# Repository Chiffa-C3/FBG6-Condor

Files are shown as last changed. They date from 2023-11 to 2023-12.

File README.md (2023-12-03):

# Проект печатной головы "Кондор" 

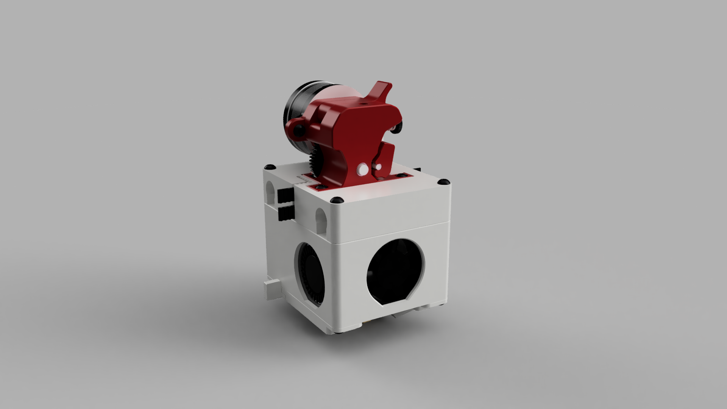
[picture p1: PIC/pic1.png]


Проект печатной головы для принтера FBG6 с поддержкой [Klicky-Probe](https://github.com/jlas1/Klicky-Probe) и фидером на основе Mini Stealthburner с быстрым отжимом филамента для более легкой замены прутка.

Используемые детали:
- Стоковый радиатор FBG6
- Гладкое биметалическое горло 21мм
- Турбинки 4010 GDSTime
- Вентилятор 3010 GDSTime
- Набор BMG шестерней [пример](https://aliexpress.ru/item/1005003334389217.html)
- Шаговый двигатель Nema 14 36STH20 [пример](https://aliexpress.ru/item/1005002717890067.html?sku_id=12000031330274970)
- 8шт Круглые магниты 5х5мм
- Микрик [пример](https://aliexpress.ru/item/4001033375208.html)
- Вплавляемые резьбовые латунные вставки М3 4-5мм длины [пример](https://aliexpress.ru/item/1005005372220229.html)

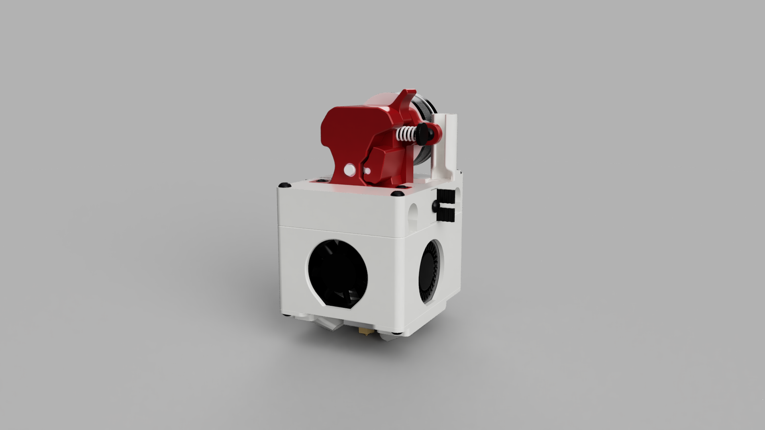
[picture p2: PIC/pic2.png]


- [Сборка проекта](https://github.com/Chiffa-C3/FBG6-Condor/tree/main/Assembly)

- [Настройка Klicky Probe](https://github.com/Chiffa-C3/FBG6-Condor/tree/main/Klicky)

Более подробно о Klicky Probe можно узнать на [странице проекта](https://github.com/jlas1/Klicky-Probe/tree/main)

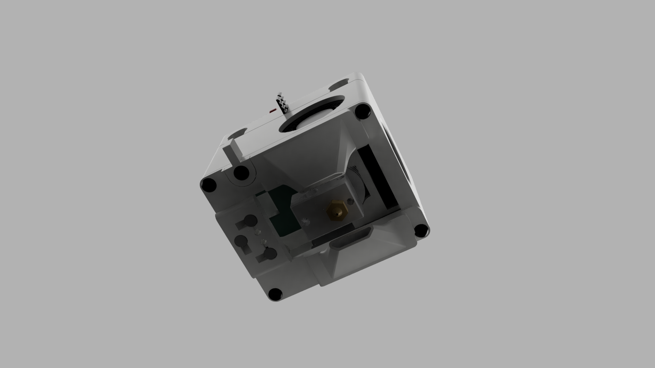
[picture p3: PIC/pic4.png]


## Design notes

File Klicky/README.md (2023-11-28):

# Настройка Klicky

Для датчика Klicky используется пин PC4 и земля.

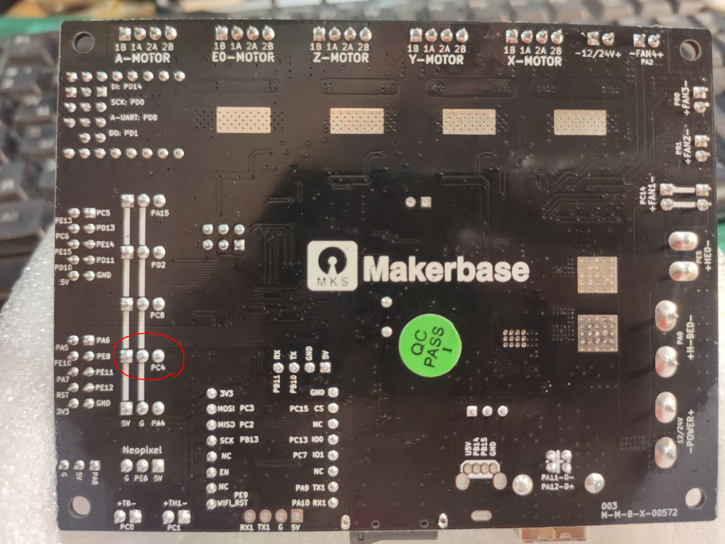
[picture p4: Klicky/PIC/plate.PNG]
plate


Файлы из папки Config скопировать рядом с файлом конфигурации прошивки Klipper `config.cfg`

Заходим в сам файл config.cfg и добавляем в начало 

```
[include klicky-variables.cfg]
[include klicky-macros.cfg]
[include klicky-bed-mesh-calibrate.cfg]
[include klicky-screws-tilt-calculate.cfg]
```

Добавляем в любом месте файла эти блоки настроек

```
[probe]
pin: ^PC4
x_offset: 2.5
y_offset: 30
z_offset: 3.8 # расстояние от кончика сопла до концевика, подбирается калибровкой через скрипт PROBE_CALIBRATE
speed: 5.0
samples: 3
sample_retract_dist: 5.0
samples_result: average
samples_tolerance: 0.1

[bed_mesh]
speed: 60
horizontal_move_z: 5
mesh_min: 7.5, 35
mesh_max: 240, 200
probe_count: 6,4
mesh_pps: 2, 2
algorithm: bicubic
fade_start: 1
fade_end: 10

[screws_tilt_adjust]                     
screw1: 25, 145
screw1_name: back left screw
screw2: 225, 145
screw2_name: back right screw
screw3: 225, 1
screw3_name: front right screw
screw4: 25, 1
screw4_name: front left screw
speed: 200
screw_thread: CW-M4
horizontal_move_z: 10
```

Находим конфигурационный блок под названием `[stepper_z]` и в нем ищем строку `endstop_pin`, комментируем ее знаком # и вставляем ниже `endstop_pin: probe:z_virtual_endstop` чтобы получилось как на примере ниже:
```
#endstop_pin: !PC8
endstop_pin: probe:z_virtual_endstop
```

Настройка позиции док станции для корректировки правильной парковки находится в файле `klicky-variables.cfg`

```
variable_docklocation_x:      168    # X Dock position
variable_docklocation_y:      210    # Y Dock position
```

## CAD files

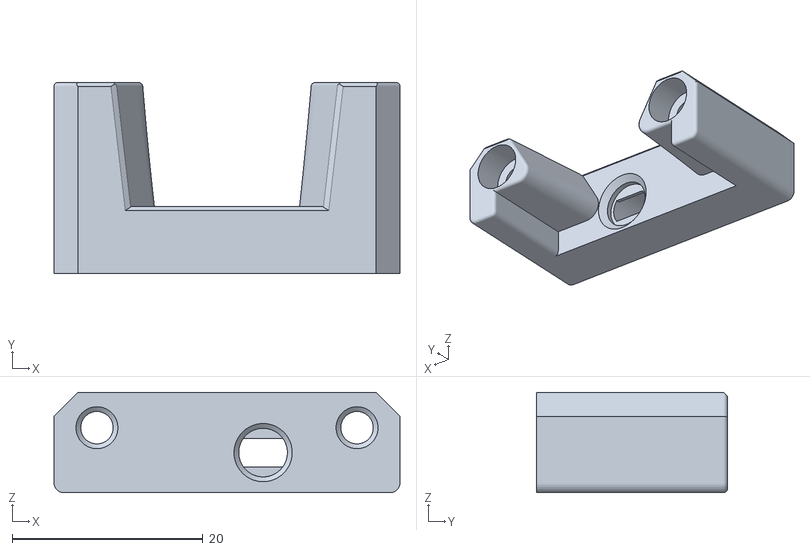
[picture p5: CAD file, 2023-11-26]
STL/Klicky/Probe Dock.stl
36.3 x 20.0 x 10.5

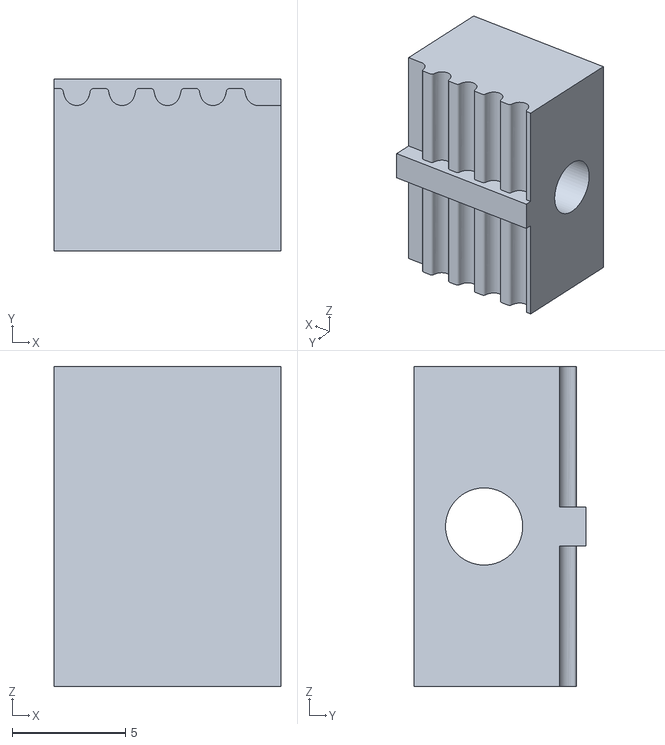
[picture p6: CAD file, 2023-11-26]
STL/Каретка/Крепление ремней.stl
10.0 x 7.60 x 14.1

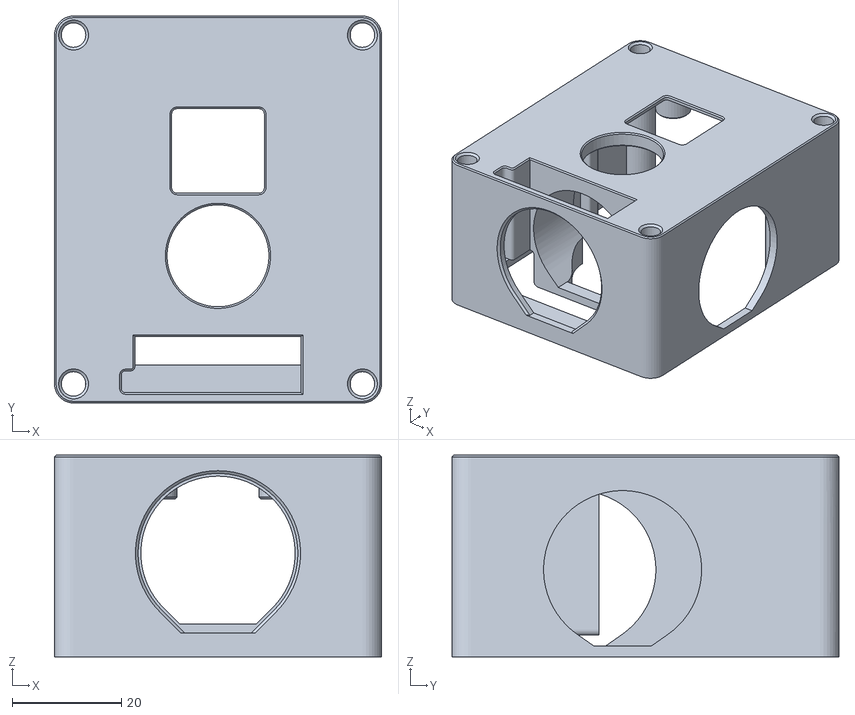
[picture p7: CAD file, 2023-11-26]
STL/Нижняя часть/Блок с вентиляторами.stl
60.0 x 71.0 x 37.0

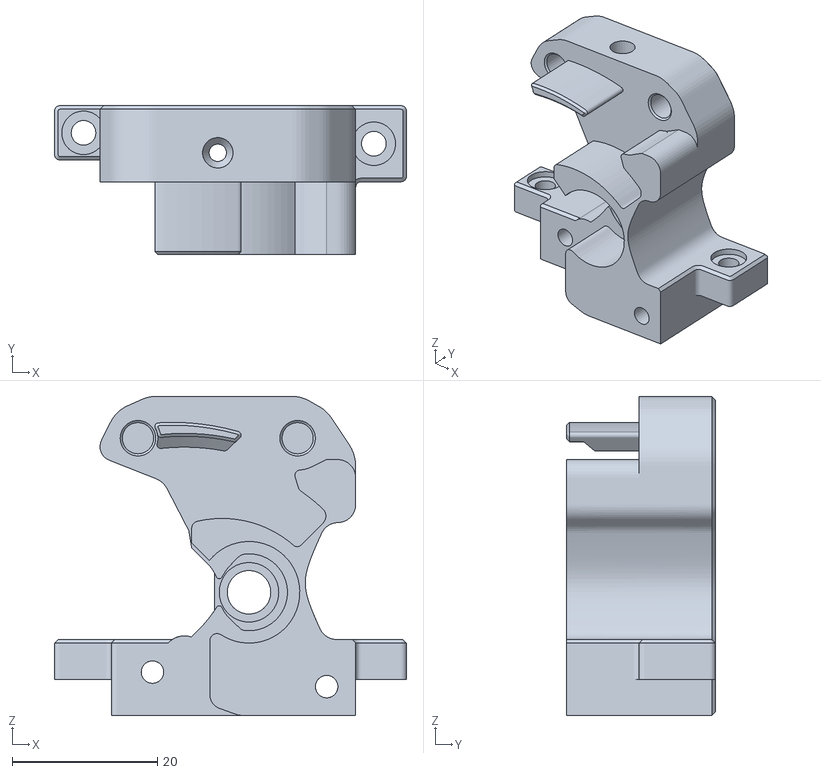
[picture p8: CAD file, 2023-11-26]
STL/Экструдер/Передняя крышка.stl
48.5 x 20.5 x 44.0

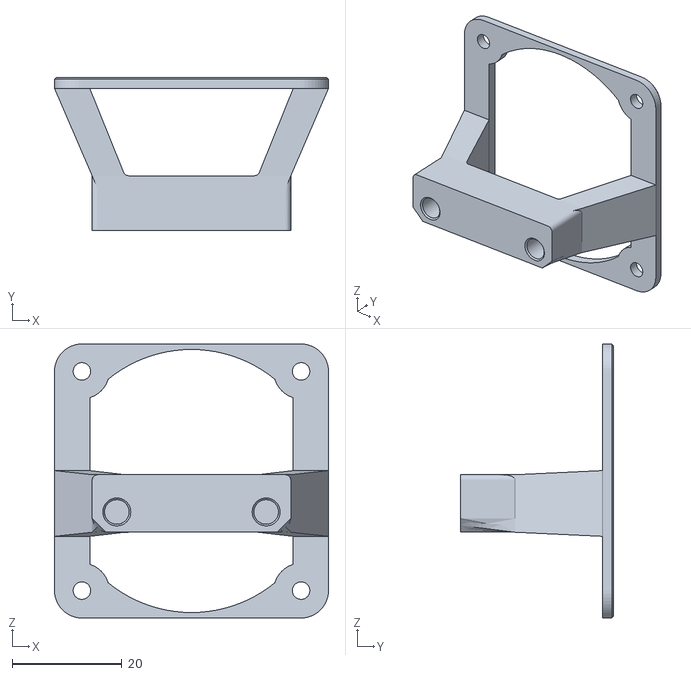
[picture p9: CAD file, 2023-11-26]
STL/Klicky/Крепление на вентилятор.stl
50.0 x 28.0 x 50.0

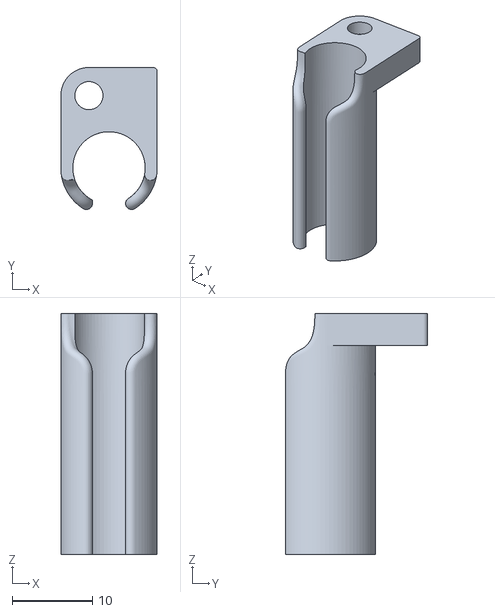
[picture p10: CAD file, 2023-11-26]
STL/Каретка/Держатель косы.stl
12.0 x 17.7 x 30.0

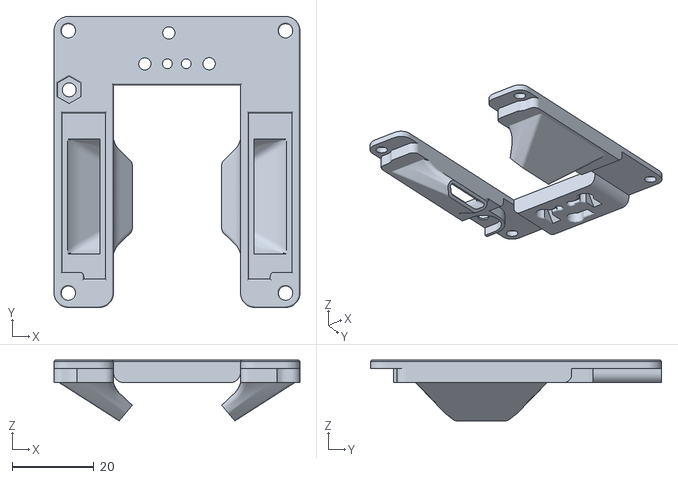
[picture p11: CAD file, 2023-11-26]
STL/Нижняя часть/Обдув.stl
60.0 x 71.0 x 14.9

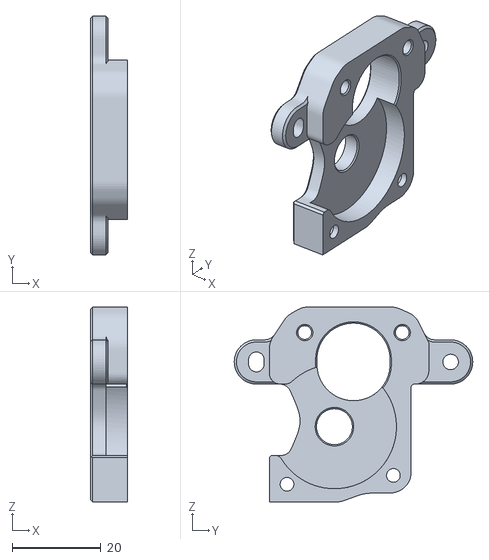
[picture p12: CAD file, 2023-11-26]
STL/Экструдер/Задняя крышка.stl
8.40 x 53.8 x 44.0

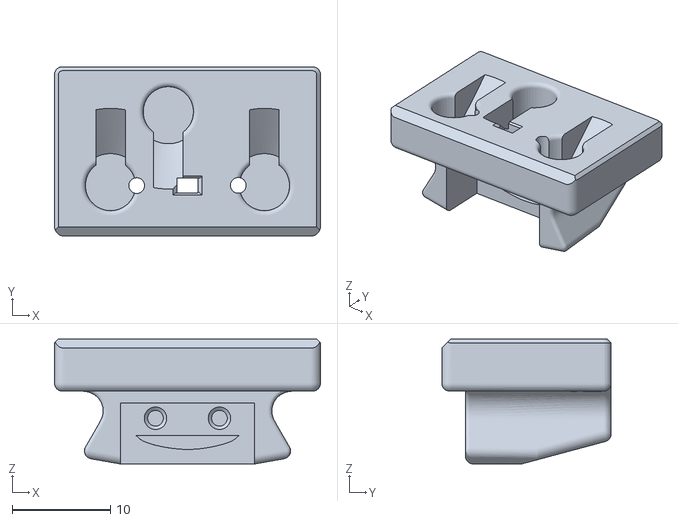
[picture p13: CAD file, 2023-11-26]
STL/Klicky/Klicky Probe.stl
27.0 x 17.2 x 12.7

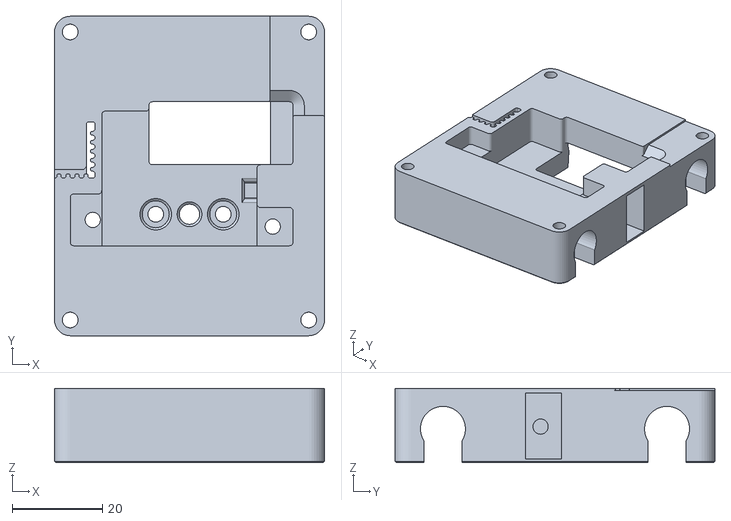
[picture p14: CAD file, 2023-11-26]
STL/Каретка/Основа каретки.stl
60.0 x 71.0 x 16.5

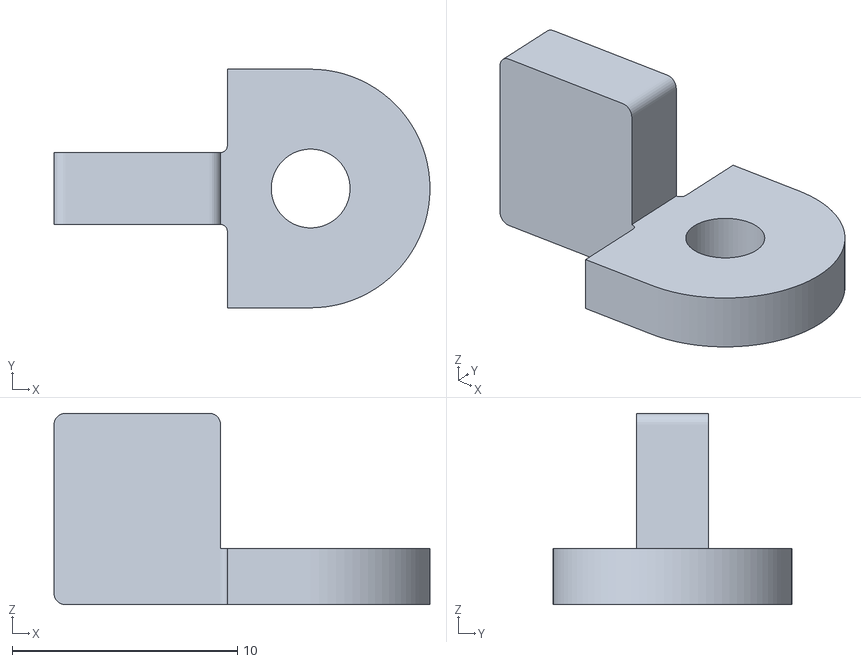
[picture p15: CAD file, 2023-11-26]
STL/Нижняя часть/Флажок концевика.stl
16.7 x 10.6 x 8.50

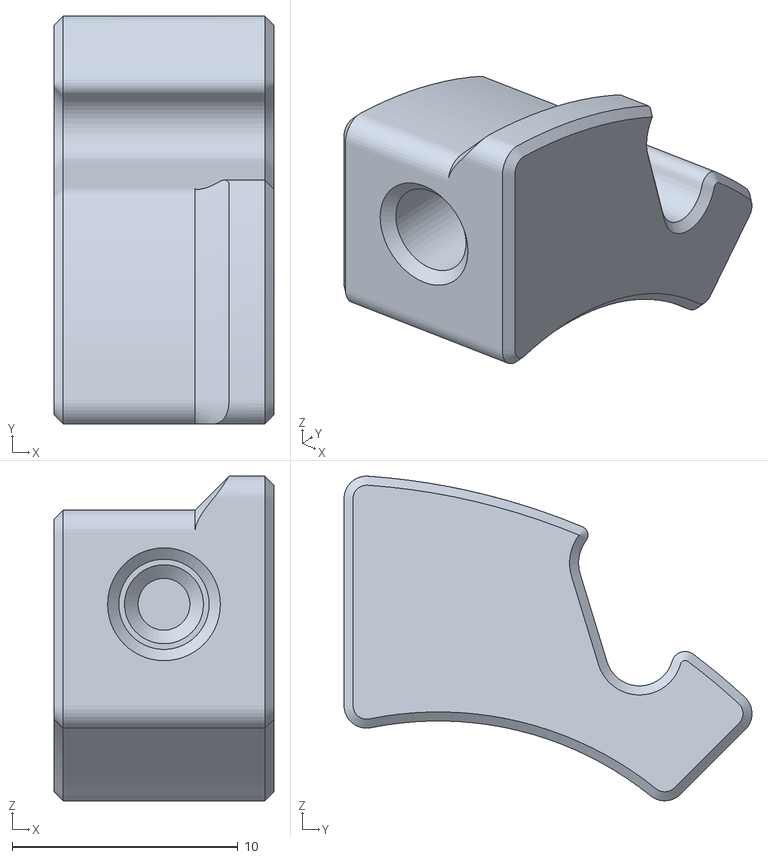
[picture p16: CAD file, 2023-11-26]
STL/Экструдер/Подвижный прижим.stl
9.75 x 18.1 x 14.4

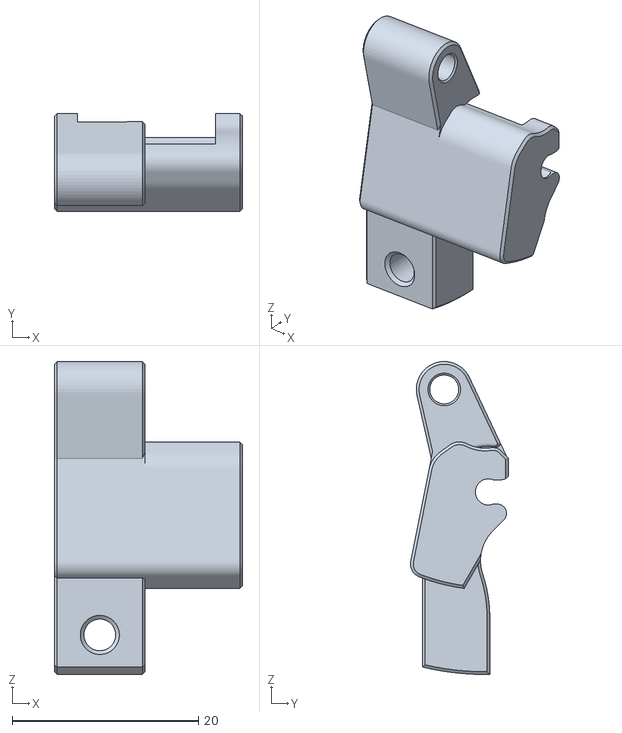
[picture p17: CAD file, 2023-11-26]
STL/Экструдер/Прижим.stl
20.2 x 10.5 x 33.6

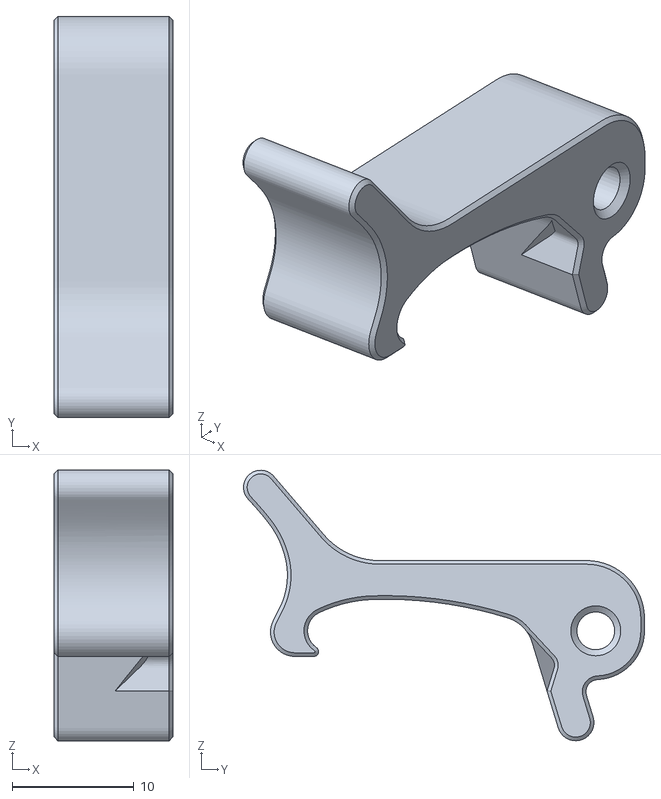
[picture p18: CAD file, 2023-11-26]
STL/Экструдер/Рычаг прижима.stl
9.75 x 32.9 x 22.2

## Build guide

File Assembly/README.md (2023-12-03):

# Сборка

## Каретка

Потребуется:
- 4шт Винт M3х20мм (20 или 25мм) для крепления блока с вентиляторами к каретке
- 1шт Винт М3х15мм для держателя ремней
- 3шт Гайка М3 для ответной части держателя ремней и крепления экструдера

***Перед установкой каретки желатательно закрепить все гайки в соответствующих пазах на каплю цианокрилата, для предотвращения выпадения.***

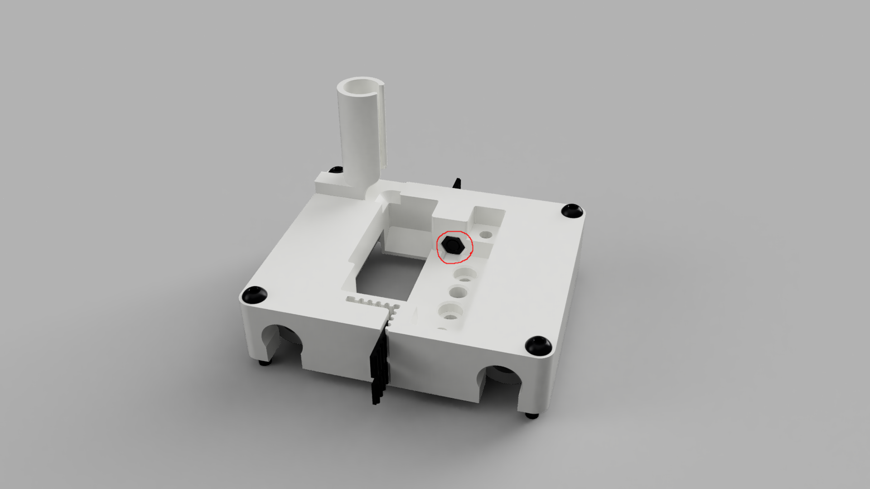
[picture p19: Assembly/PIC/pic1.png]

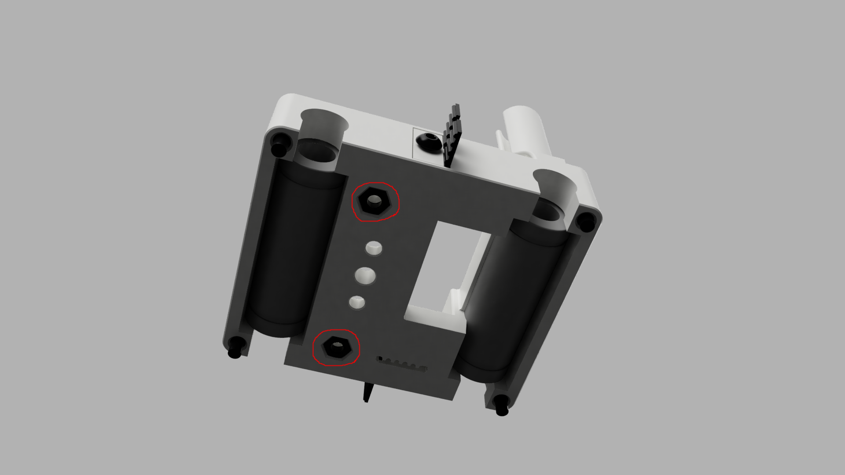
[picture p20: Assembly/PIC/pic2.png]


## Корпус для вентиляторов

Потребуется:
- 10шт Вплавляемых резьбовых латунных вставок М3 4-5мм длины [пример](https://aliexpress.ru/item/1005005372220229.html)

## Сопла и крепление Klicky

Потребуется:
- 5шт Винт M3х5мм
- 1шт Гайка М3
- 3шт Магниты круглые 5х5мм
- Провод (опционально с разьемом) для подключения Klicky [пример](https://aliexpress.ru/item/1005005334563700.html)

Провода, которые будут использоваться для подключения датчика Klicky, зачищаем на свободных концах, продеваем в предусмотренные отверстия, загибаем в пазы, а затем в отверстие запресовываются магниты прижимая провода (для надежности фиксации магнитов можно использовать каплю цианокрилата на дно отверстия).

***При запресовывании магнитов, обратите внимание на их полярность, для корректного примагничивания Klicky один из трех магнитов должен быть развернут другим полюсом наружу (см. картинку ниже, красные и синие метки отображают положение полюсов магнитов)***

***После установки магнитов, не забудьте закрепить флажок концевика на соответствующее крепление!***

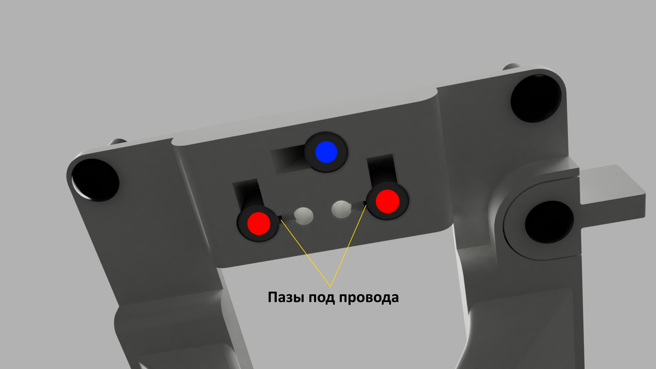
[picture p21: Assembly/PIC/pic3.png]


## Фидер

Потребуется:
- 4шт Винт M3х20мм для сборки корпуса
- 2шт Винт M3х10мм (6-10мм) для крепления шагового двигателя
- 2шт Винт M3х15мм для крепления фидера к каретке
- Набор BMG шестерней [пример](https://aliexpress.ru/item/1005003334389217.html)
- Шаговый двигатель Nema 14 36STH20 [пример](https://aliexpress.ru/item/1005002717890067.html?sku_id=12000031330274970)
- 5шт Вплавляемых резьбовых латунных вставок М3 4-5мм длины [пример](https://aliexpress.ru/item/1005005372220229.html)

Перед началом сборки, вплавить в переднюю и заднюю крышку, а так же в подвижный прижим, латунные резьбовые вставки (см. картинки ниже) 

***прим. на задней крышке отверстия для вставок находятся на внешней стороне***

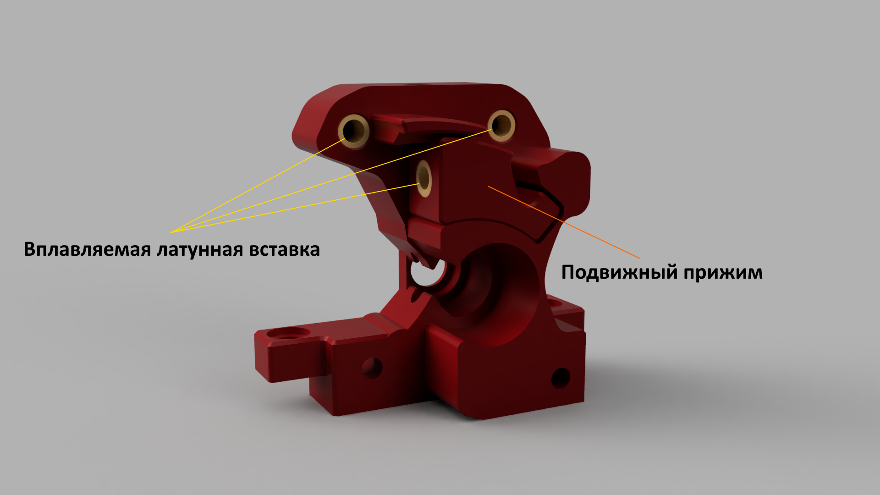
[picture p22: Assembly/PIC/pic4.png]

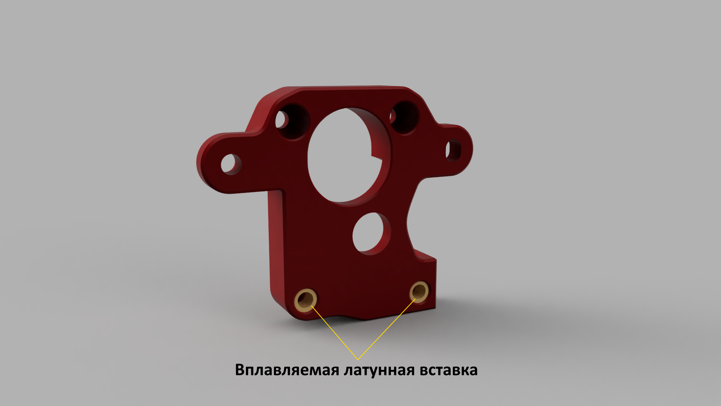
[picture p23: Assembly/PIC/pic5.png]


Устанавливаем в лапку прижима филамента ответную часть шестерни, в нижние отверстия в передней крышке закладываем винты, далее устанавливаем на место подвижный прижим, лапку прижима и основную собранную ось экструдера вместе с подшипниками. 

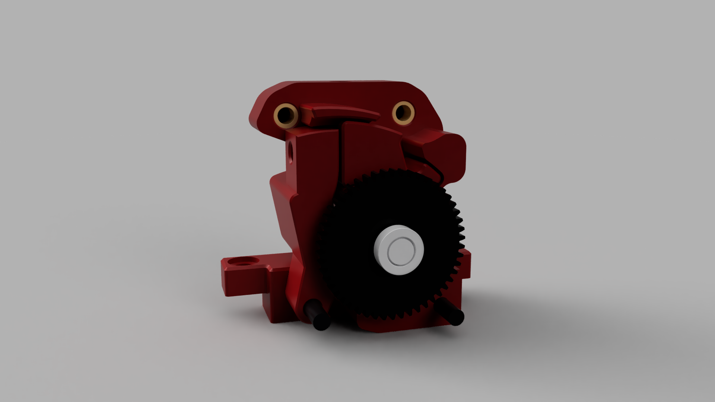
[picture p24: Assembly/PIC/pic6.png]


Ставим на место заднюю крышку и привинчиваем ее не затягивая до конца, далее устанавливаем рычаг прижима и верхние два винта, скручиваем все вместе до конца.

***В процессе затягивания всех винтов важно не переусердствовать, иначе можно потерять подвижность лапки прижима и откидывающегося рычага!***

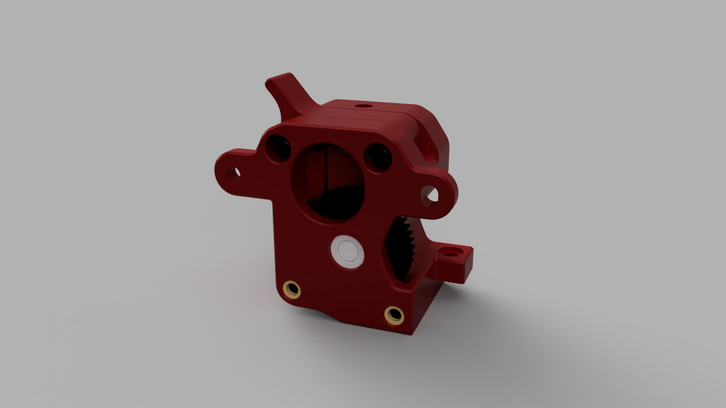
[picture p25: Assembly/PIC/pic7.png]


Далее прикручивается шаговый двигатель и регулируется его прижим к большой шестерне для устранения люфта, после этого можно вкручивать винт с пружиной для регулировки прижима.

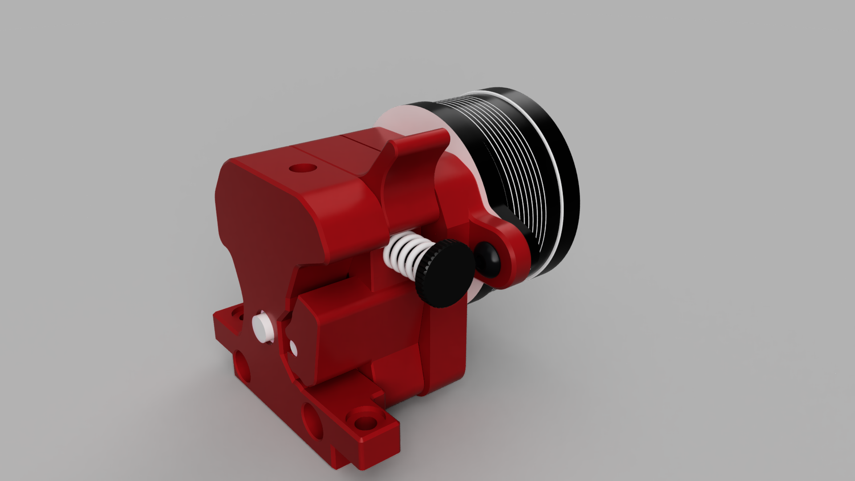
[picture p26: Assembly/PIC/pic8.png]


## Датчик Klicky

Потребуется:
- 2шт М2 Саморез под шестигранник [пример](https://aliexpress.ru/item/1005004457944548.html?gatewayAdapt=glo2rus&sku_id=12000029239680241)
- Микрик [пример](https://aliexpress.ru/item/4001033375208.html)
- 4шт Магниты круглые 5х5мм

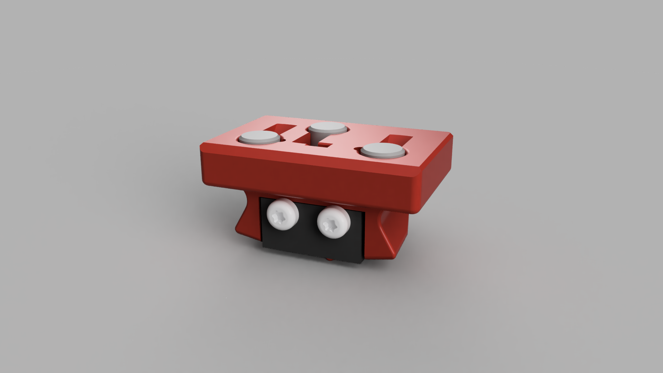
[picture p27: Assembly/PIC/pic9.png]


Прикручиваем микрик к основанию датчика и впресовываем магниты в 4 отверстия (для надежности фиксации магнитов можно использовать каплю цианокрилата на дно отверстия).
Для корректной работы датчика требуется чтобы крайние ножки микрика имели хороший контакт с магнитами. После сборки можно проверить контакт с помощью мультиметра, замерив крайние магниты прозвонкой. В не нажатом состоянии - цепь замкнута, в нажатом - разомкнута.

***Не забудьте убедиться в правильной полярности магнитов относительно крепления на голове!***

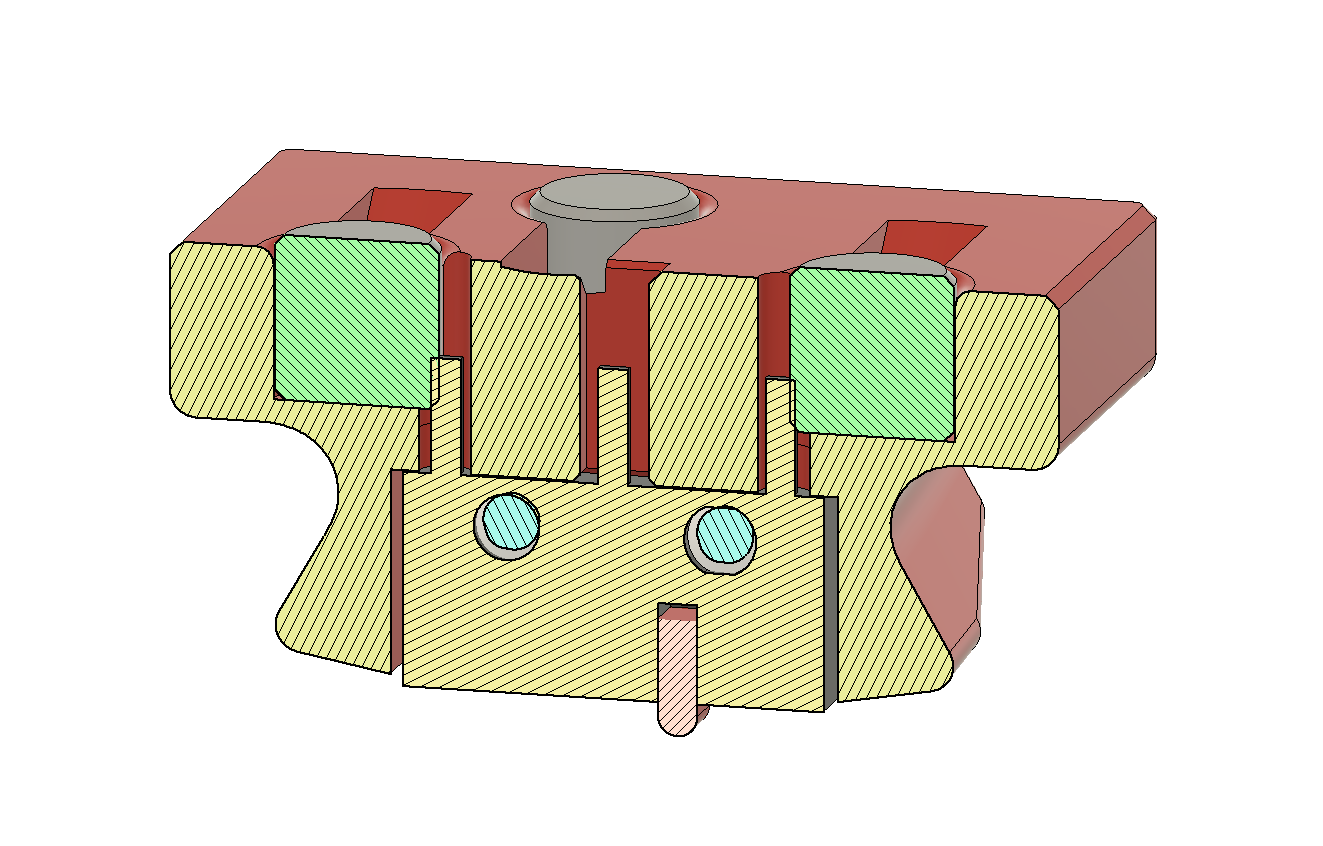
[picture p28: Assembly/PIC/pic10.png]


## Док станция

Потребуется:
- 2шт Вплавляемых резьбовых латунных вставок М3 4-5мм длины [пример](https://aliexpress.ru/item/1005005372220229.html)
- 2шт Винт M3х20мм для сборки корпуса
- 1шт Магнит круглый 5х5мм

В одну из половинок детали устанавливается магнит (перед установкой, проверьте полярность относительно датчика), после детали скручиваются между собой  и крепятся поверх вентилятора на задней стенке принтера.

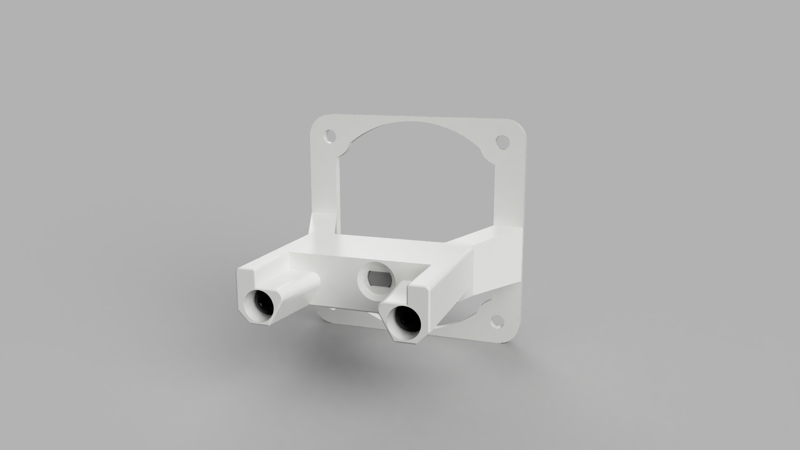
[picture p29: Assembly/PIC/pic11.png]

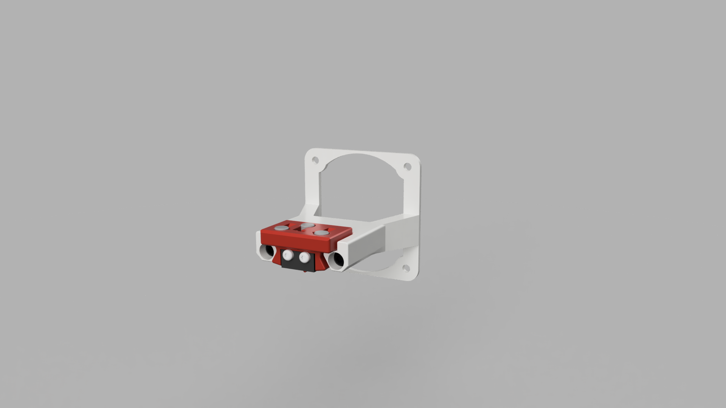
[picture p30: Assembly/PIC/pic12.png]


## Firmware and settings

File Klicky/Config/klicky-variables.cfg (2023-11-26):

# This macro was provided by discord user Garrettwp to whom i give my thanks for sharing it with me.
# I have tweaked it a lot.
# They are based on the great Annex magprobe dockable probe macros "#Originally developed by Mental,
# modified for better use on K-series printers by RyanG and Trails", kudos to them.
# That macro as since evolved into a klipper plugin that currently is pending inclusion in klipper,
# more information here, https://github.com/Annex-Engineering/Quickdraw_Probe/tree/main/Klipper_Macros
# User richardjm revised the macro variables and added some functions, thanks a lot
# by standing on the shoulders of giants, lets see if we can see further
#
# the current home for this version is https://github.com/jlas1/Klicky-Probe
# the 1000 values below is to give an error instead of doing something wrong, hopefully, this won't be used is a printer larger than 1 meter

[gcode_macro _User_Variables]
variable_verbose:             True    # Enable verbose output
variable_debug:              False    # Enable Debug output
variable_travel_speed:         100    # how fast all other travel moves will be performed when running these macros
variable_move_accel:          1000    # how fast should the toolhead accelerate when moving
variable_dock_speed:            50    # how fast should the toolhead move when docking the probe for the final movement
variable_release_speed:         75    # how fast should the toolhead move to release the hold of the magnets after docking
variable_z_drop_speed:          20    # how fast the z will lower when moving to the z location to clear the probe

variable_safe_z:         	    8    # Minimum Z for attach/dock and homing functions
# if true it will move the bed away from the nozzle when Z is not homed
variable_enable_z_hop:        True    # set this to false for beds that fall significantly under gravity (almost to Z max)

variable_max_bed_y:            200    # maximum Bed size avoids doing a probe_accuracy outside the bed
variable_max_bed_x:            250    # maximum Bed size avoids doing a probe_accuracy outside the bed

# if a separate Z endstop switch is in
# use, specify the coordinates of the switch here (Voron).
# Set to 0 to have the probe move to center of bed
variable_z_endstop_x:         0
variable_z_endstop_y:         0

#Check the printer specific documentation on klipper Dock/Undock configuration, these are dummy values
#dock location
#Тут пишем координаты док станции
variable_docklocation_x:      168    # X Dock position
variable_docklocation_y:      210    # Y Dock position
variable_docklocation_z:      -128   # Z dock position (-128 for a gantry/frame mount)

#The following variables are used if the dock is deployed and retracted via a servo motor
variable_enable_dock_servo:  False    # Set to true if your klicky dock is servo-controlled
variable_servo_name:        'NAME'    # The name of the dock servo defined in printer.cfg under [servo]
variable_servo_deploy:          10    # This EXAMPLE is the value used to deploy the servo fully
variable_servo_retract:         11    # This EXAMPLE is the value used to retract the servo fully (initial_angle in [servo] config)
variable_servo_delay:          250    # This is a delay to wait the servo to reach the requested position, be carefull with high values

#Dock move, final toolhead movement to release the probe on the dock
#it's a relative move
Variable_dockmove_x:            30
Variable_dockmove_y:             0
Variable_dockmove_z:             0

#Attach move. final toolhead movement to attach the probe on the mount
#it's a relative move
Variable_attachmove_x:           0
Variable_attachmove_y:          17
Variable_attachmove_z:           0

#Umbilical to help untangle the umbilical in difficult situations
variable_umbilical:          False    # should we untangle the umbilical
variable_umbilical_x:           15    # X umbilical position
variable_umbilical_y:           15    # Y umbilical position

# location to park the toolhead
variable_park_toolhead:       True    # Enable toolhead parking
variable_parkposition_x:         1
variable_parkposition_y:         1
variable_parkposition_z:        10    # -128 excludes Z - Park only on X-Y

variable_version:                1    # Helps users to update the necessary variables, do not update if the variables above are not updated

#Below this remark, you normally do not need to configure
#Attach move2
Variable_attachmove2_x:          0    # intermediate toolhead movement to attach
Variable_attachmove2_y:          0    # the probe on the dock
Variable_attachmove2_z:          0    # (can be negative)

variable_home_backoff_x:        0    # how many mm to move away from the X endstop after homing X
                                      # this is useful for the voron v0 to enable the toolhead to move out of the way to allow an unstricted Y homing
variable_home_backoff_y:        0    # how many mm to move away from the Y endstop after homing Y

variable_override_homing:       ''    # configures what axis to home first
                                      #  '' = default klicky behavior (tries to avoid the hitting the dock)
                                      # 'X' = forces X to home first
                                      # 'Y' = forces Y to home first
                                      
variable_dock_on_zhome:       True    # docks the probe on Z Homing if not necessary (avoids hitting the bed on some printers       

variable_bypass_probe_docking:        False                               

# Do not modify below
gcode:
    {% set Mx = printer['configfile'].config["stepper_x"]["position_max"]|float %}
    {% set My = printer['configfile'].config["stepper_y"]["position_max"]|float %}
    {% set Ox = printer['configfile'].config["probe"]["x_offset"]|float %}
    {% set Oy = printer['configfile'].config["probe"]["y_offset"]|float %}
    {% set Oz = printer['configfile'].config["probe"]["z_offset"]|float %}

    # If x, y coordinates are set for z endstop, assign them
    {% if z_endstop_x != 0 or z_endstop_y != 0 %}
        SET_GCODE_VARIABLE MACRO=_Probe_Variables VARIABLE=z_endstop_x VALUE={ z_endstop_x }
        SET_GCODE_VARIABLE MACRO=_Probe_Variables VARIABLE=z_endstop_y VALUE={ z_endstop_y }

    # if no x, y coordinates for z endstop, assume probe is endstop and move toolhead to center of bed
    {% else %}
        SET_GCODE_VARIABLE MACRO=_Probe_Variables VARIABLE=z_endstop_x VALUE={ (Mx * 0.5) - Ox }
        SET_GCODE_VARIABLE MACRO=_Probe_Variables VARIABLE=z_endstop_y VALUE={ (My * 0.5) - Oy }
    {% endif %}
